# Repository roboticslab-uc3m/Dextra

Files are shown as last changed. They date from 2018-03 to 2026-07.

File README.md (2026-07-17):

# Dextra

Dextra is a printable robotic hand with the size of a human hand. This project was initially started by A. Villoslada to build a replicable and low cost alternative to current robotic hand prostheses. However, I think this device has more potential uses, for example in robotics research (humanoid robotics, mobile platforms with manipulation capabilities) or in education, fields that could benefit from the existence of a cheap and easy to repair robotic hand, a robotic device that is replicable and hackable, and simple but functional.

<p align="center">

</p>

There is more information about Dextra on its [hackaday.io project page](https://hackaday.io/project/9890-dextra).

## Dextra TPMG90

J. Gago Industrial Technologies Engineering Bachelor's Degree Final Project comprises the development and integration of an anthropomorphic robotic hand in the humanoid robot TEO. TEO is a household companion developed by RoboticsLab, at Carlos III University of Madrid, whose current robotic hands lack the necessary functionality for the tasks that require high manual dexterity, like fabric manipulation.

<p align="center">
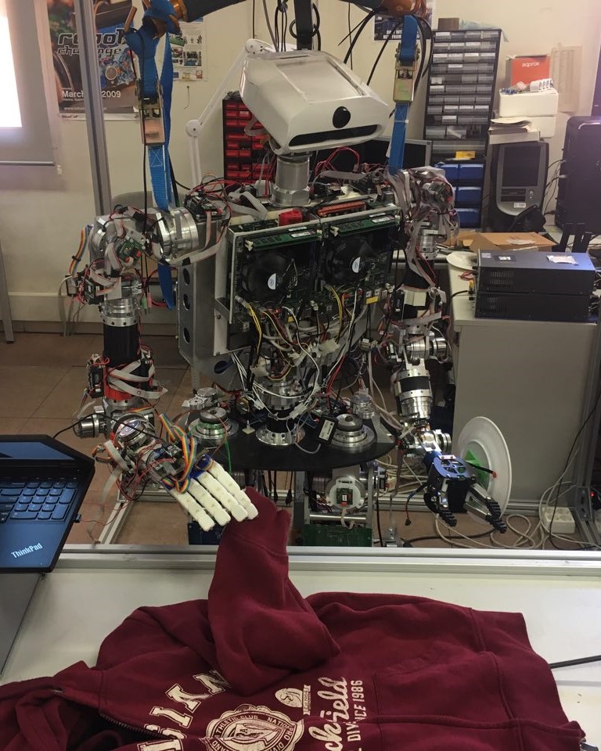
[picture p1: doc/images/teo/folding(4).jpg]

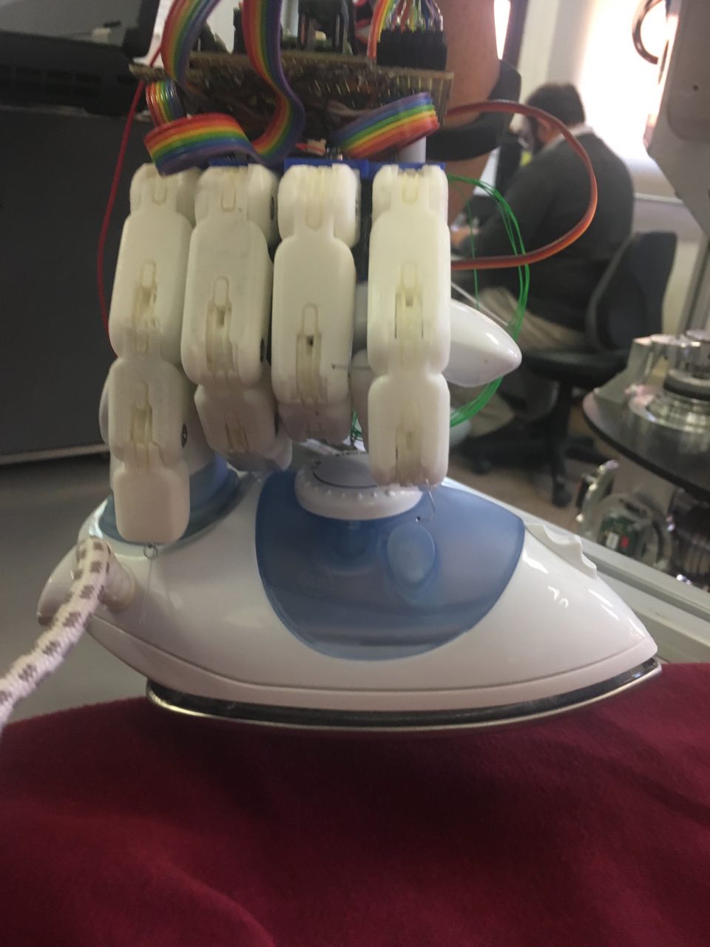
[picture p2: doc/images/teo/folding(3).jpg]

</p>

The scope of the proposed objectives is achieved through the development and study of several versions of the selected hand at the mechanical, electronic and software level. Multiple experiments are developed to evaluate the effectiveness of the robotic hand. In addition, the regulatory technical framework and the socio-economic environment of the project are evaluated, so that it complies satisfactorily with the established restrictions and adjusts to the current social and economic context.

<p align="center">
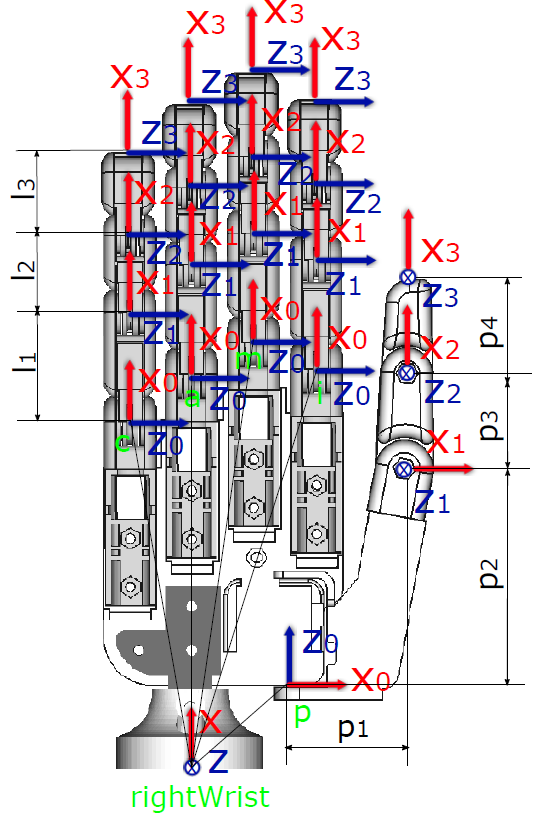
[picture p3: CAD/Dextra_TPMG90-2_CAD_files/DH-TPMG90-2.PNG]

</p>

The project is oriented to numerous additional studies around their behavior in the humanoid, contemplating the expansion of the TEO functions in relation to the versatility provided by his new fully functional hands.

<p align="center">
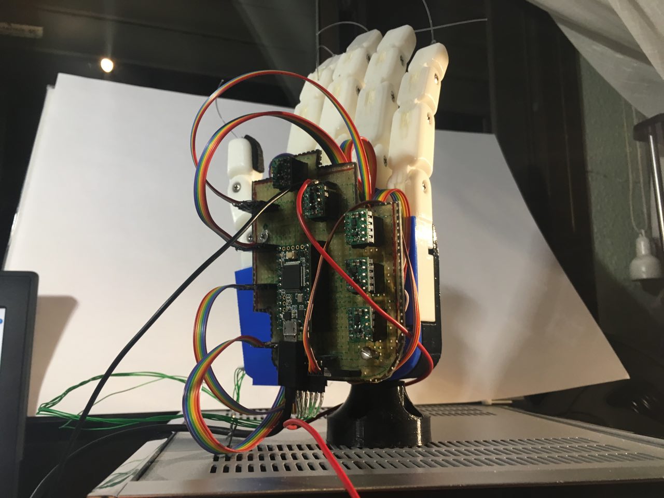
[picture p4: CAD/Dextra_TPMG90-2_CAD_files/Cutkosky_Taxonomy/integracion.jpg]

</p>

## Dextra TPMG90S

Miguel Alache Manchado followed up on Jennifer Gago's work in his Bachelor's Degree Final Project (Industrial Electronics Engineering and Automation), notably improving the 3D CAD and PCB designs. This iteration is dubbed TPMG90S due to the replacement of the TPMG90 servomotor with this new model.

Although compatibility with TEO is preserved, the aim was to mount this hand on the ABB CRB 15000-5 "GoFa" collaborative robot arm.

<p align="center">
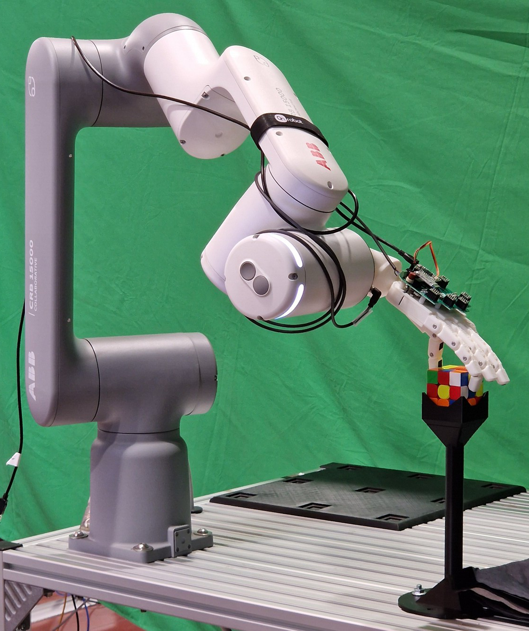
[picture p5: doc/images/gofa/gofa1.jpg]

</p>

## Useful documents

The assembly instructions for the original Dextra can be found [here](doc/dextra_assembly_instructions.pdf).

## Project index

* [CAD](CAD) - Printable parts
* [Control](Control) - Code for different control methods (EMG, GUI)
* [doc](doc) - Documentation files
* [Firmware](Firmware) - Main program and libraries that make Dextra move
* [PCB](PCB) - PCB design files
* [Schematics](Schematics) - Electronic schematics of Dextra Original, TPMG90-1 and TPMG90-2

## License

<a rel="license1" href="https://www.gnu.org/licenses/gpl-3.0.html">GNU License</a>  

Code is licensed under the [GPL v3 License](https://www.gnu.org/licenses/gpl-3.0.html). The rest of the work is licensed under the [Creative Commons Attribution-ShareAlike 4.0 International License](http://creativecommons.org/licenses/by-sa/4.0/).

## See also

* [dextra-yarp-devices](https://github.com/roboticslab-uc3m/dextra-yarp-devices) - YARP plugins for Dextra control board

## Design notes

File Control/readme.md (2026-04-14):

The Dextra Control GUI is designed using [Kivy](https://kivy.org/#home). Besides having Python installed, this library and its dependencies are required to run the application. The application uses both the *.py* and the *.kv* files, and they need to be in the same folder.

To run the control GUI, connect the microcontroller running the Dextra firmware to a USB port of the computer, and run:

```bash
~/Dextra$ cd Control
~/Dextra/Control$ python3 DextraControl.py
```

First, the device to which we want to communicate (the microcontroller running the Dextra firmware) has to be selected from a dropdown list. Once the desired device is selected (in this case the one connected to COM4; in this example the app is running on a Windows PC), we click on the connect button. If there is no device connected to the PC, or no device is selected from the dropdown list, an error message is displayed.

<p align="center">
        
</p>

If the connection is successful, we can select the *Control panel* tab. In this tab, we can control the position of each finger and the abduction angle of the thumb. The position values can be inputted by using the text boxes or by moving the sliders.

<p align="center">
    
</p>

To stop communicating with the microcontroller, we select the *Connection* tab and click the disconnect button.

<p align="center">
    
</p>

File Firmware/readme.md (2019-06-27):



To upload the firmware to one of the supported boards, use [platformio](http://platformio.org/).

For Teensy 3.1 (Arduino-compatible board):
```bash
~/Dextra$ cd Firmware/Teensy31
~/Dextra/Firmware/Teensy31$ platformio run --target upload
```

Make sure you have sufficient rights to interface with the Teensy H/W. This can be accomplished by copying `49-teensy.rules` to `/etc/udev/rules.d/`.

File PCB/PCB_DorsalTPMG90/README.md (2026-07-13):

# PRINTED CIRCUIT BOARD FOR DEXTRA TPMG90-2
## OBJECTIVE
The main objective is to design a Printed Circuit Board (PCB) to replace the breadboard, shown bellow, in the back of the right robotic hand of the humanoid robot TEO. A PCB is a board or card that electrically connects and mechanically supports electrical components. These connections are made with a series of conductive tracks or traces (usually copper ones). This copper is laminated onto or in between sheets of non-conductive material like fiberglass.

<p align="center">
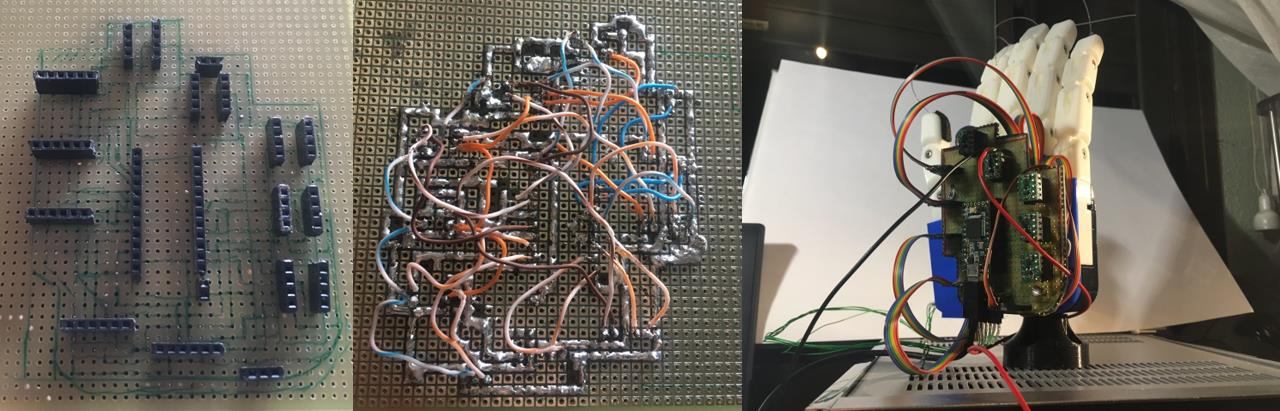
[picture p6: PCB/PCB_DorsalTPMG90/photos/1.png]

</p>

## CONSIDERATIONS

Points below were taken into account during the design process:
* PCB shape and size
* User interfaces
* PCB layers
* Ground layers
* Traces width

Regarding PCB traces:
* 45° angles shorten the electrical path between components.
* High speed logic signals (above 200 MHz) can get reflected off the back of the angle, Causing interference.
* 90o has the likelihood of being etched narrower than your standard trace width.
* 90o traces back might not be fully etched, could cause shorts.

<p align="center">
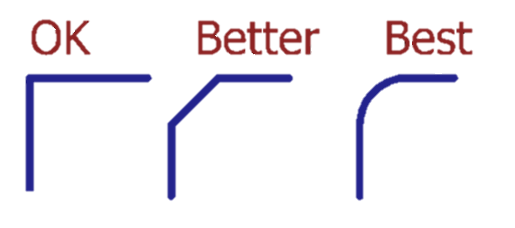
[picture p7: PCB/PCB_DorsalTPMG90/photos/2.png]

</p>

## MATERIALS

The design of the PCB is going to be done using KiCad, an open-source software tool which can be considered mature enough to be used for the successful development and maintenance of complex electronics boards.

<p align="center">
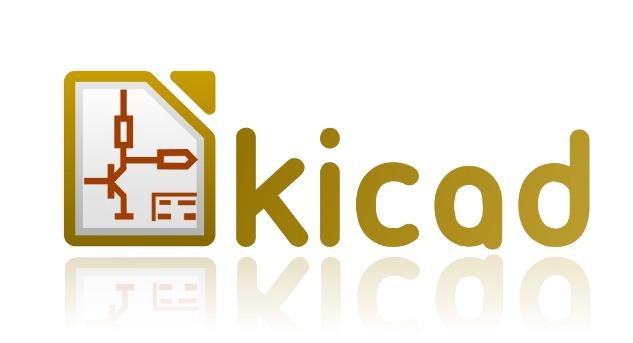
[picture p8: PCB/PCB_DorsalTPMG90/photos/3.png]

</p>

## WORKFLOW

The KiCad workflow is comprised of two main tasks: drawing the schematic and laying out the board. Both a schematic component library and a PCB footprint library are necessary for these two tasks. In the following figure, the workflow followed during this project is shown.

<p align="center">
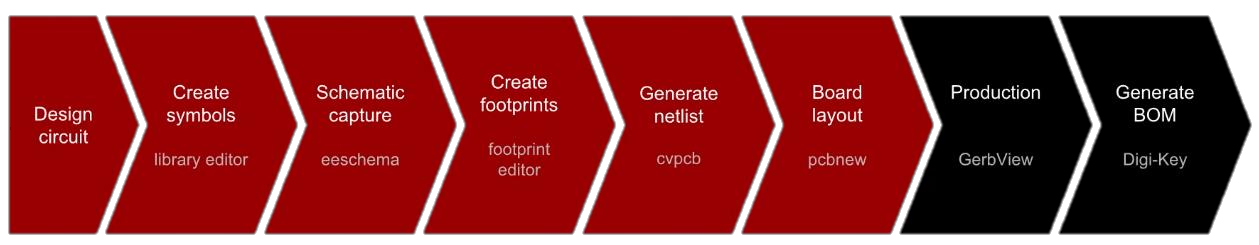
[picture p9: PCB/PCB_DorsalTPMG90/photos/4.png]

</p>

Any PCB design is divided in three main steps:
* Schematics design
* PCB design (routing, components and PCB dimensions)
* BOM list (Bill of materials): actual components to be used (in case connectors of any type have to be considered: USB, expansion jumper connectors...)

### 1. SCHEMATIC DESIGN

It is assumed that each components is a box with inputs and outputs. The schematic contains the connections between the pins of the boxes without considering the dimensions of any component. To start with the design it is needed the datasheet with the pinout description for each component (in our case the drivers, the Servo and the microprocessor).

* DRV8838 Single Brushed DC Motor Driver Carrier

<p align="center">
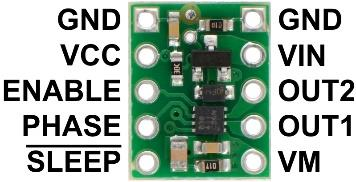
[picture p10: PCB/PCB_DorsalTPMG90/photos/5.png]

</p>

* Microcontroller: Teensy 3.2

<p align="center">
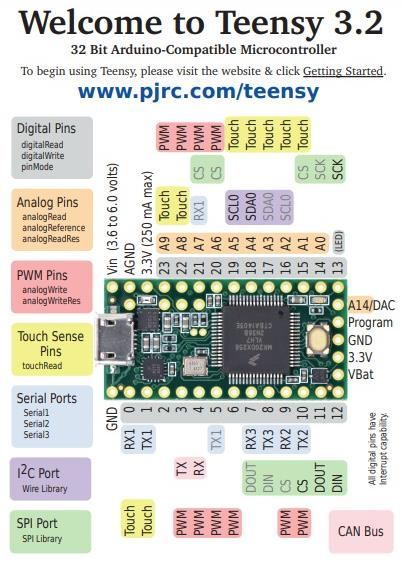
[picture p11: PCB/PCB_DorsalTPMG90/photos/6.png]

</p>

* Servo TowerPro MG90 (directly connected to the PCB)

<p align="center">
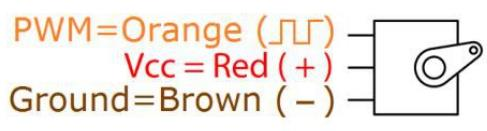
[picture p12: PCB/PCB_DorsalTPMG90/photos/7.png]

</p>

The starting point of this project is based on the connections shown in the schematic depicted in the figure bellow, and available in this GitHub repository (Dextra/Schematics/DEXTRA_TPMG90-2.png). In this design each component is represented as a pair of standard connectors (one for each side of the component). Although it can be easily understood, it is preferable to create specific symbols for each component to facilitate PCB layout in following steps.

<p align="center">
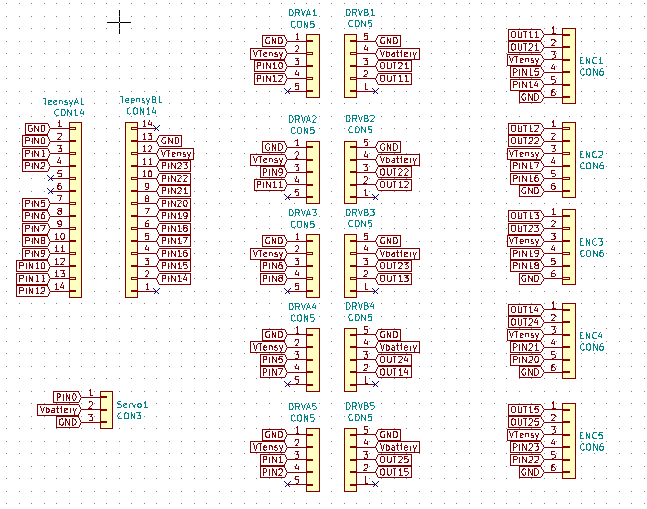
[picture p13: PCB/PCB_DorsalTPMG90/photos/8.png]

</p>

The symbols for the components are stored in two different schematic libraries located in “Project folder/Libraries/dorsalSchematic_Components/ and are named: <b>DRV8838_Pololu.lib</b> and <b>teensy.lib</b>. In the case of the driver, the components were created manually using KiCad and in the case of the Teensy it was downloaded from a GitHub [repository](https://github.com/XenGi/teensy_library). The pair of figures bellow show the schematic symbols for Teensy 3.2 and Pololu Driver, respectively.

<p align="center">
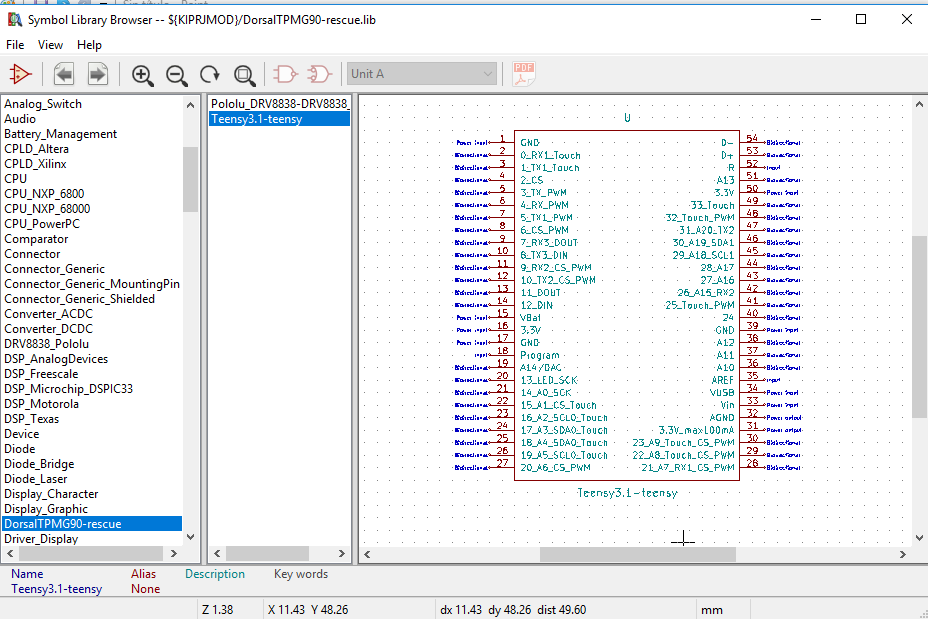
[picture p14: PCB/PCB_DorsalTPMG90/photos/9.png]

</p>

<p align="center">
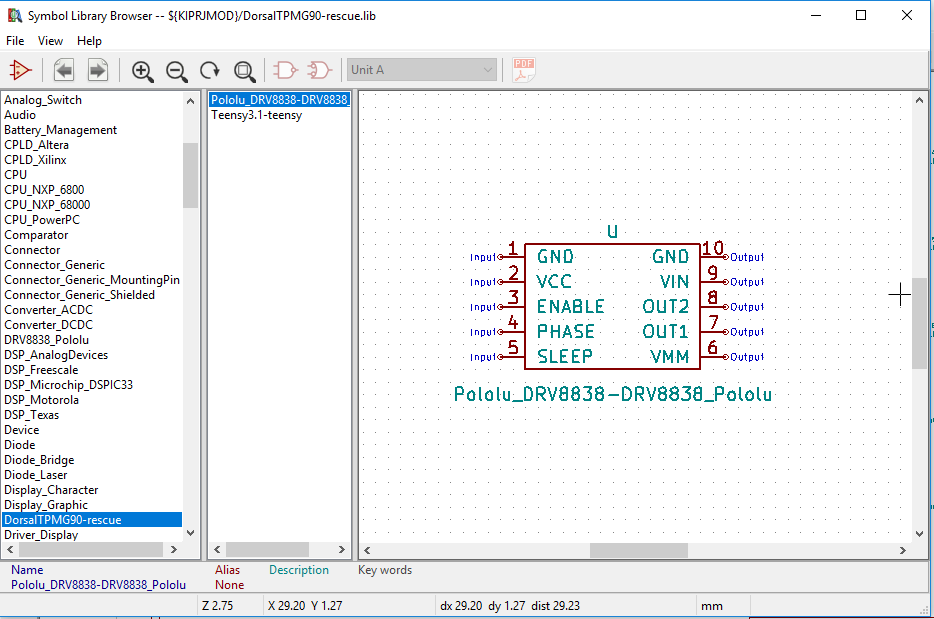
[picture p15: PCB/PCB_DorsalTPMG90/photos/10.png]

</p>

The final schematic is shown bellow. Standard connectors have been used for the 6 encoders, the Servo and the battery input. For the drivers and the Teensy the symbols already mentioned are shown. In order to establish the connections global labels, no connection flags, and power ports have been used. Final step is <b>to annotate the components and create the Netlist</b> which is later import in the PCB design.

<p align="center">
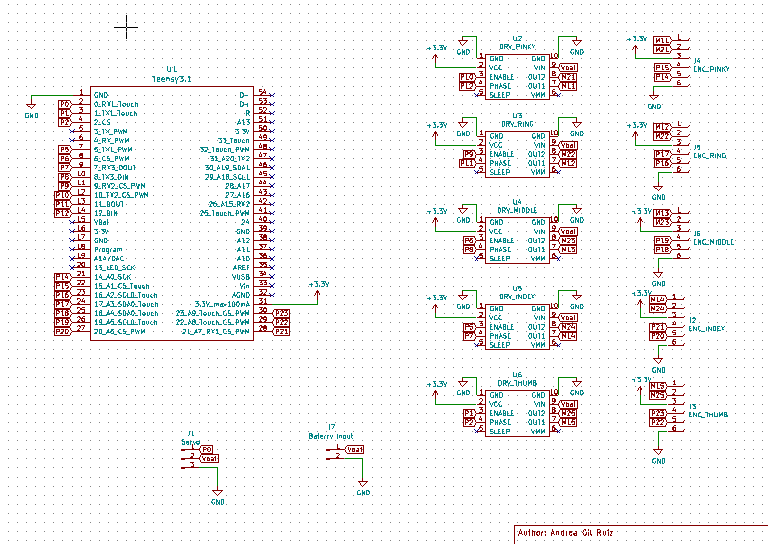
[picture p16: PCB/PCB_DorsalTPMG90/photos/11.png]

</p>

### 2. PCB DESIGN

This is probably the most difficult part of the project.. Steps followed are:

1. Assign footprints to each symbol in the schematic design.
2. Import Netlist with the connections
3. PCB layout design:
    1. Draw PCB edges and holes according to CAD specifications.
    2. Place each component in specific locations and orientations to facilitate trace routing
    3. Route components: use front and back Cu layers because there are too many connections; use vias when needed; increase trace width depending on maximum current specifications.
    4. Fill Front and Back Cu layers with GND and VCC (+3.3V), respectively.
4. Define Design Rules according to Oshpark prototypes and run Design Rules Check at the end of the layout to avoid errors.
5. Place text and Logos to indicate component name and orientation during assembly.

The main difference between footprints and symbols is that footprints define the physical interface between the PCB and the component (land pattern) and include other information (outline, polarization mark, reference...) while symbols are just a representation of the component (they abstract its function) showing the pins.

In order to assign each correspondent footprint to the symbols, a new library of footprints has been created with the corresponding footprints for the drivers and the Teensy. In the folder “Project folder */Libraries/dorsalPCB_Components.pretty* / (folders ending in .pretty are recognized by KiCad as footprint library) are 3 footprints. The footprint for the driver has been
created manually using the dimension specification in its datasheet (shown below).

<p align="center">
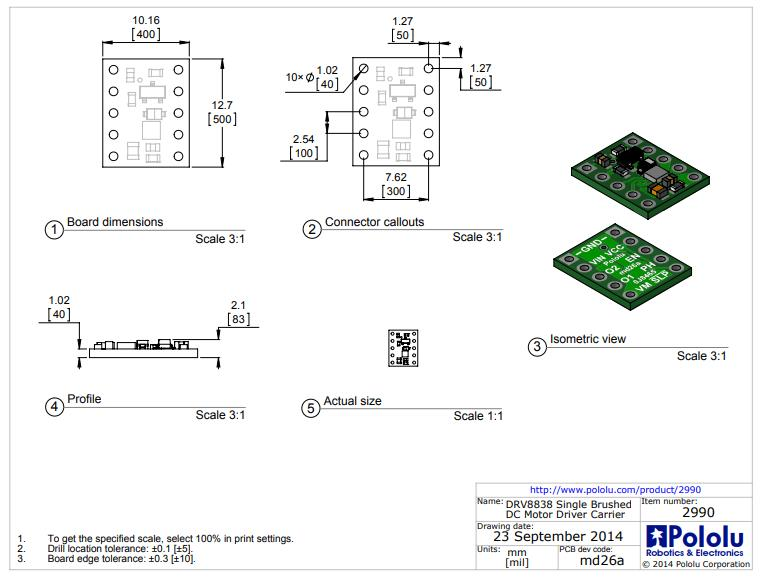
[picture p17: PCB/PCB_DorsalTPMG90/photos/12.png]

</p>

<p align="center">
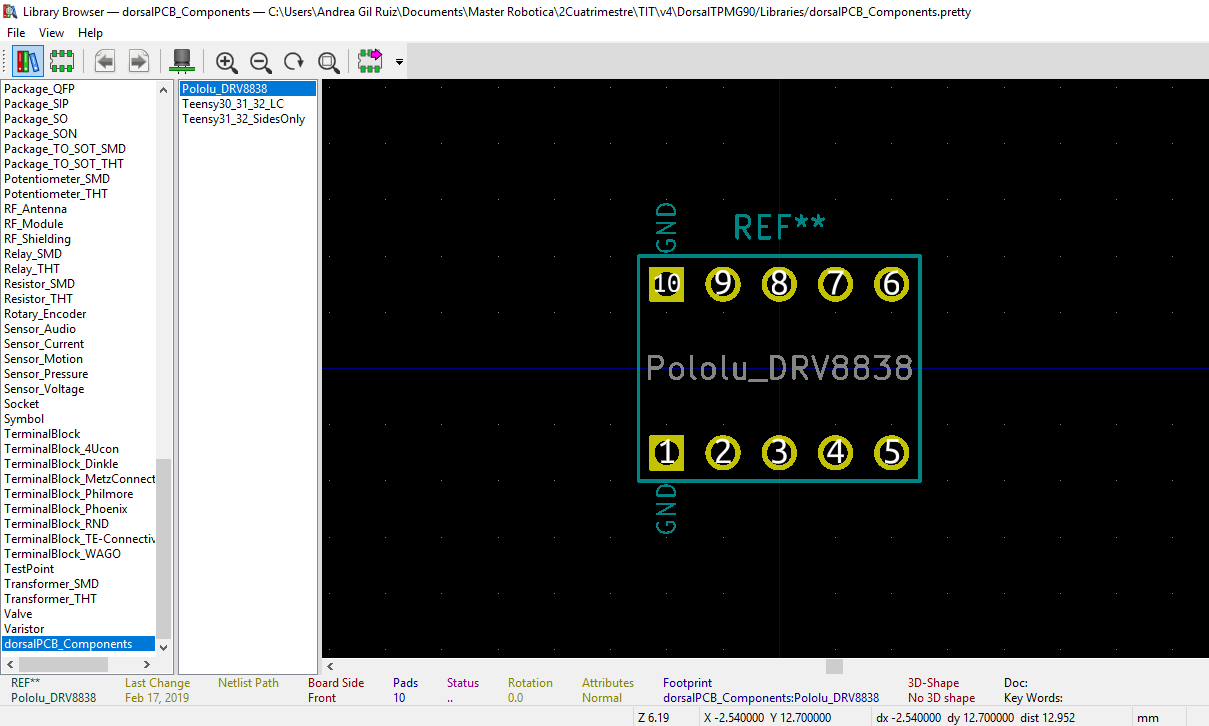
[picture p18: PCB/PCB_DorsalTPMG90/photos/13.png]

</p>

The footprint for the Teensy has been downloaded for the GitHub [repository](https://github.com/XenGi/teensy.pretty) and edited in KiCad to delete the pins which are not used in the design. Only pins on sides have been kept, as shown in the figures below, to facilitate routing.

<p align="center">
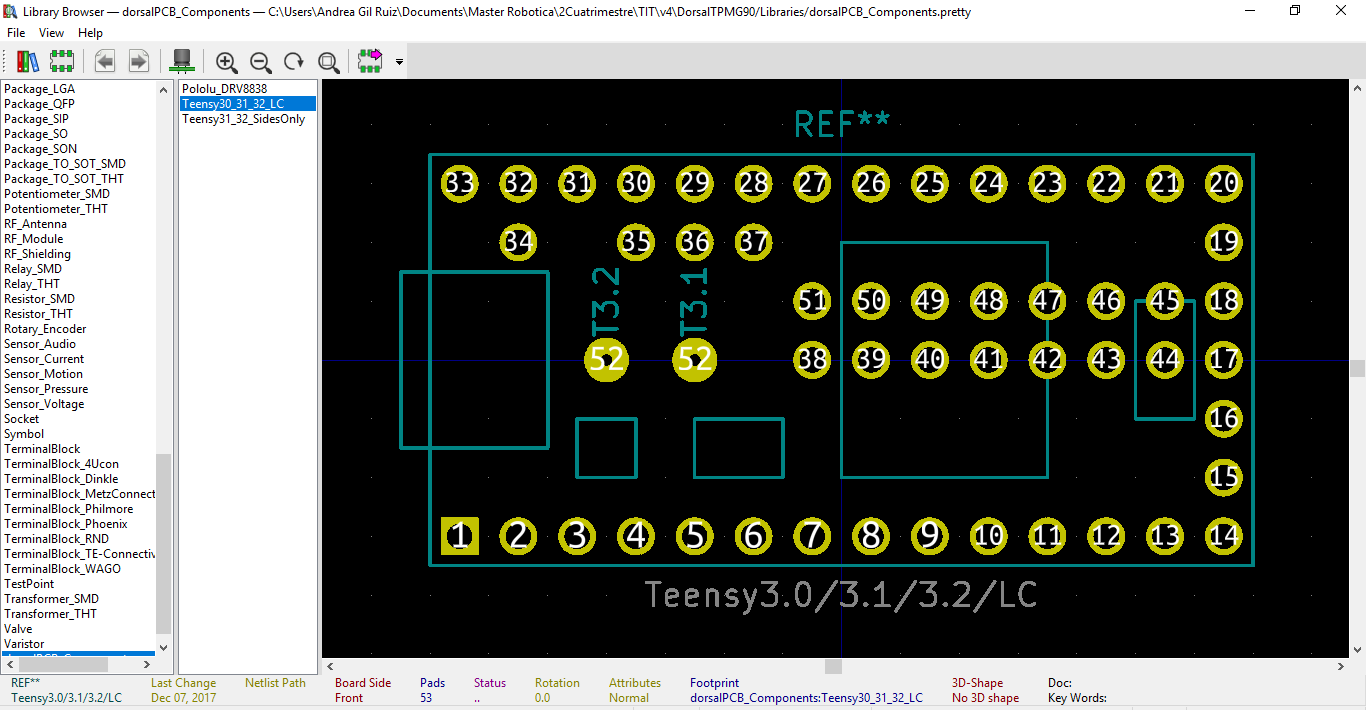
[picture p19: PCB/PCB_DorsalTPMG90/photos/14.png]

</p>

<p align="center">
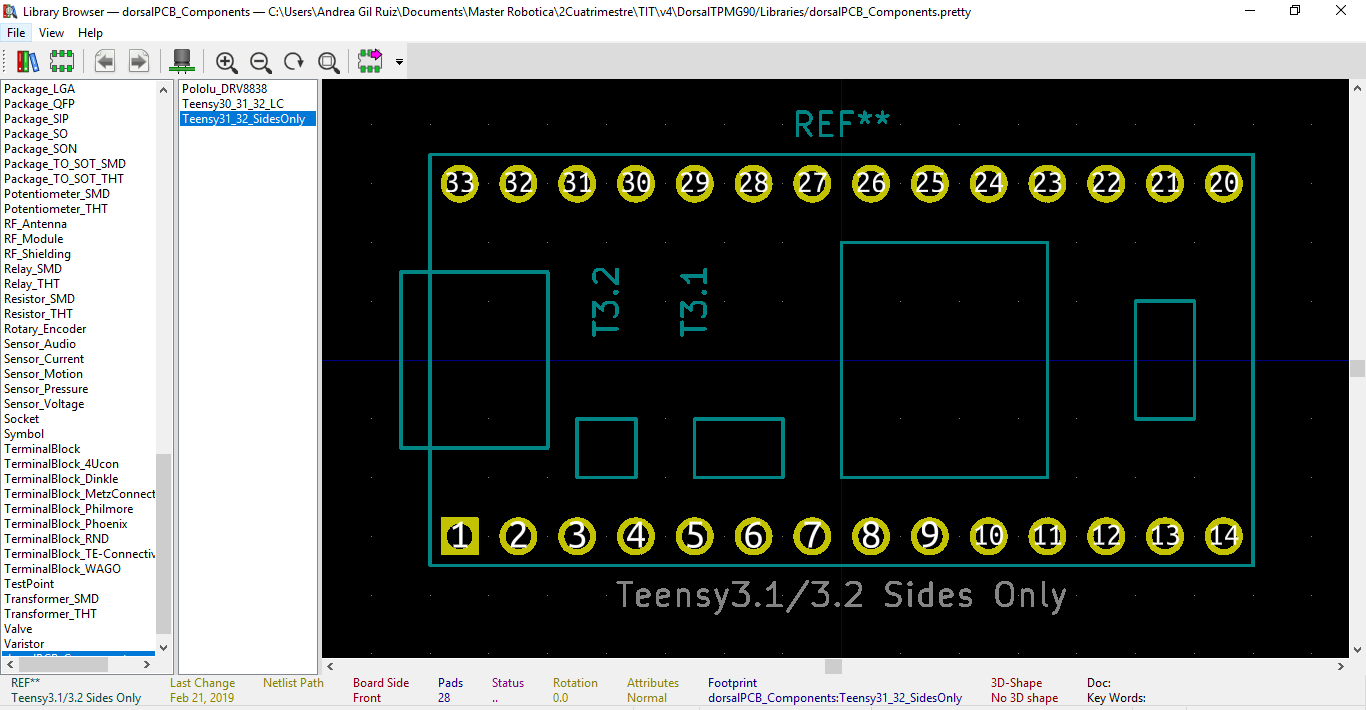
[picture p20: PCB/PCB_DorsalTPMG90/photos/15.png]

</p>

Once the footprints have been assigned it is possible to read the schematic Netlist and start designing the PCB. Steps follow for the design are explained below:

* Place the components into the space of the designed board. For this step, the CAD file of the dorsal is used (path:  Dextra/Dextra_TPMG90-2_CAD_files/dorsalTPMG90-2.FCStd). The dimensions are specified in the figures below.

<p align="center">
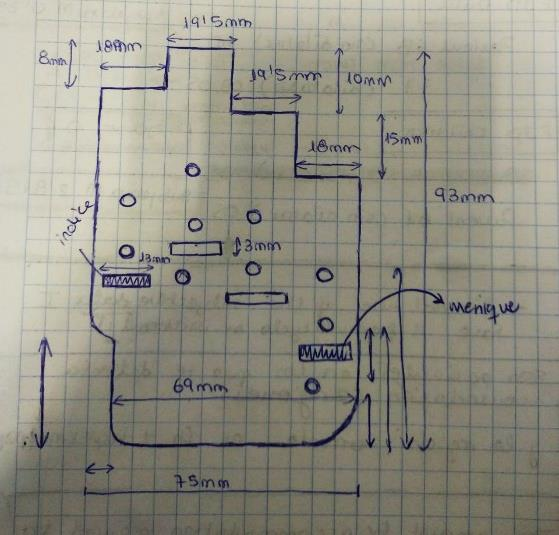
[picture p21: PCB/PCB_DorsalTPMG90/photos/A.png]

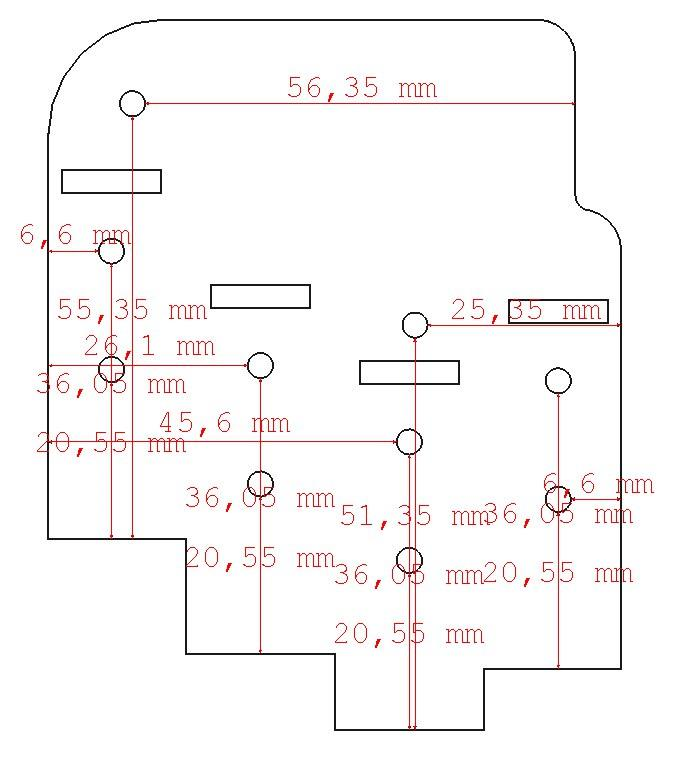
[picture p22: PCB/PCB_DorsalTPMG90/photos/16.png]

</p>

<p align="center">
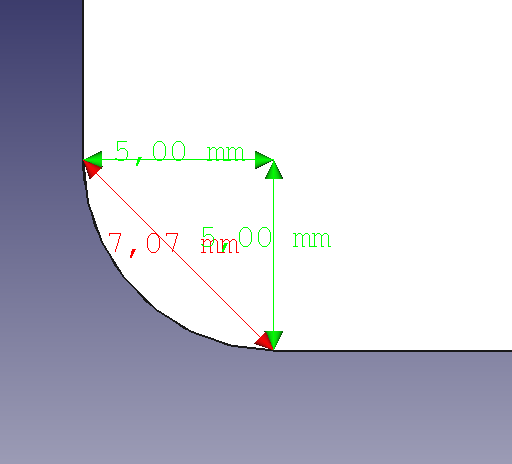
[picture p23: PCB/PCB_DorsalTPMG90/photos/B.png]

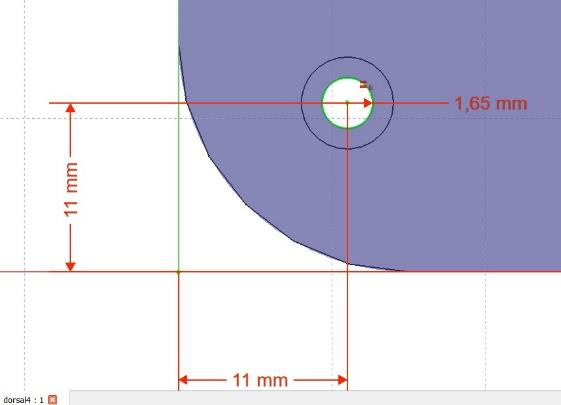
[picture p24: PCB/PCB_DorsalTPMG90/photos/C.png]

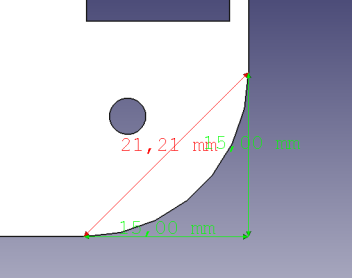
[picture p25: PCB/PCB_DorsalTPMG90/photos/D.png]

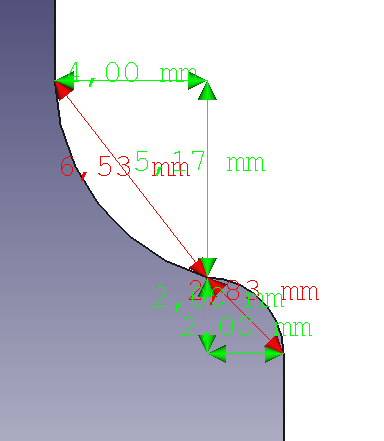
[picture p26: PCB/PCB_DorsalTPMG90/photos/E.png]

</p>

The shape and distribution have been drawn in the edge cap layer (See Annex) using graphic lines and circles (and using different grids to draw an accurate design). (Defining the outline)

<p align="center">
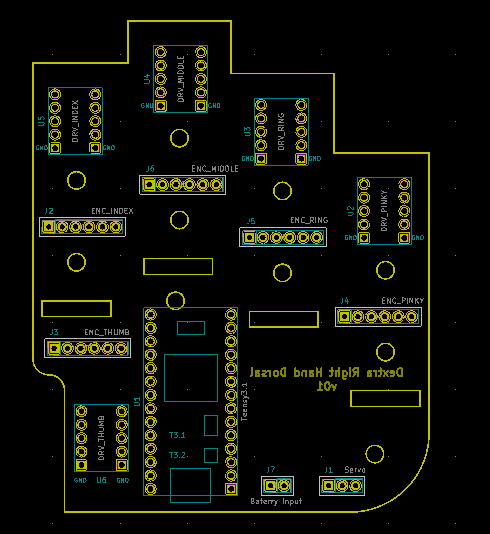
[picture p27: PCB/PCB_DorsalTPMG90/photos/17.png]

</p>

The next step is drawing traces to make air wires disappear (checking always the design rules check DRC). If there are any issues with the layout (such as traces being too close together) it will appear there, as well as the connections which should be made with copper traces. Traces have been drawn in front cupper layer and back cupper layer, using only 45 degree bends to make connections. Considerations:

* Power lines /Power traces (VBat in our case) are larger than signal traces as they need to carry much more current. Theoretically the trace supplying power needs to support up to 1.7 A, according to Pololu DRV8838 datasheet. Trace width calculator (0.676 mm).
* Connect first pads which are close together.
* Traces have not been used to connect the Ground and VCC (+3.3V) nodes as a Cu pour will be used to make those connections. A copper pour is an area in the PCB that is filled with copper. The pour is usually connected to DC voltage (Back Cu layer in our design) and Ground (Front Cu layer in our design). Its use reduces radio emissions from traces
that are surrounded by this pour especially in circuits with higher frequencies.
* It is not possible to draw a trace across another trace or a pad, use Vias in these situations.
* Use 45º angles (many older board houses could only manufacture straight lines on that angles). Also, when you get up to higher frequencies (above 1GHz) reflections could be introduced with hard 90º bends (not our case).
* Try to avoid acute angles where copper connects (older board manufacturing processes used harsh chemicals to etch away copper). Traces with bends of less than 90º would capture some of these chemicals (acid trap).

<p align="center">
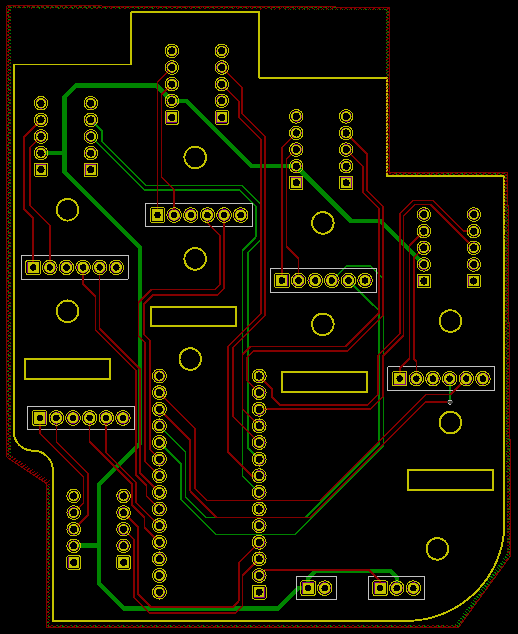
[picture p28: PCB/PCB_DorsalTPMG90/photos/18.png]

</p>

In the current design two pour areas have been used: one for the power (+3V3) in the back layer and the ground in the front layer. Also, connections between pads in both layers and one vias. The final result is shown in the next figure.

<p align="center">
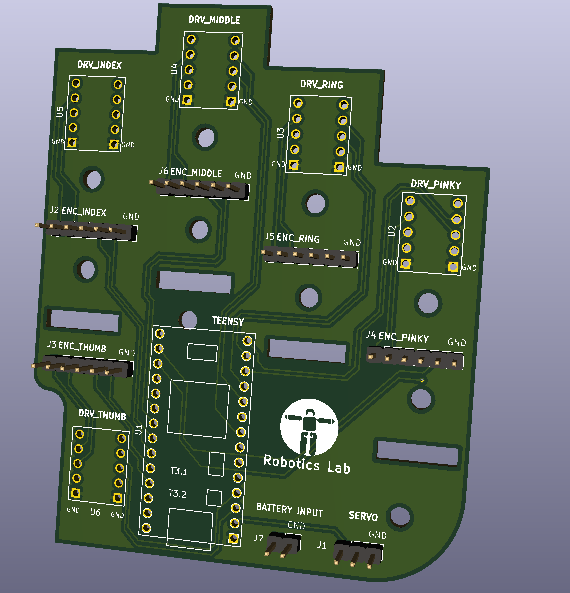
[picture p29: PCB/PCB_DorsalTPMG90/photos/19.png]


</p>

## Annex: Layers information

In KiCad the following layers are available.

* Layers that have a front and back version start with F. (for front) and B. (for back)
* The F.Cu and B.Cu layers are the copper layers
    * If there are additional copper layers they use the names In [number].Cu by default
    * The names for copper layers can be changed by the designer.
* F.Silk and B.Silk define artwork on the silkscreen layers.
    * Typically this is the white artwork printed on the board.
* F.Mask and B.Mask define the area free of [soldermask](https://en.wikipedia.org/wiki/Solder_mask) 193.
    * It is the negative of the resulting film that covers the board.
* F.Paste and B.Paste define the area that will be covered with [solder paste](https://en.wikipedia.org/wiki/Solder_paste) 88 (In datasheets often called stencil)
    * Used for [reflow soldering](https://en.wikipedia.org/wiki/Reflow_soldering) 32 of surface mounted devices.
* Edge.cuts: This layer is used to communicate with the manufacturer what the final board shape should look like.
    * The edge-cut is must not contain self intersections
    * Polygons on the edge-cut must be continuous and closed.
    * It is allowed to have internal cutouts
* F.Adhes and B.Adhes are layers to define adhesive (=glue) areas.
    * Only needed if components are on the bottom side during reflow soldering. (And even with components on the bottom it is not always needed. Check with your manufacturer if you need to define it for your board.)
* F.CrtYd and B.CrtYd are used to define a courtyard area.
    * The courtyard defines where no other component should be placed.
        * The size of this area depends on your manufacturing capabilities.
        * It also depends on your needs. (If you want the possibility to rework the pcb, you might need a larger area compared to when you do not plan to do this.)
        * The rules used in the official lib are defined in the [KLC - Rule](http://kicad-pcb.org/libraries/klc/F5.3/) F5.3 87 and are closely aligned to industry standards.
    * In KiCad 4.0.x courtyard violations are not checked by the design rule check
* F.Fab and B.Fab are documentation layers.
    * These are intended to be used for communicating with board assembly houses and for user documentation.
* Dwgs.User and Cmts.User are used for user drawings and comments.
    * In the official lib this layer is used to communicate with the user of footprints. (Example to tell them where to place keepout areas as they are not directly supported by KiCad in footprints)
* Eco1 and Eco2 are layers with no specific defined purpose. (The user can use them for whatever they want. They are not used in footprints supplied by the official lib.)
* Margin layer: Is there to define a margin relative to the edge cut.
    * There is no DRC check to verify that no copper feature violates the margin definition.

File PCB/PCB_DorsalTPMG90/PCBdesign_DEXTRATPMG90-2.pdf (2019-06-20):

## PRINTED CIRCUIT BOARD FOR DEXTRA TPMG90-2

OBJECTIVE

The main objective is to design a Printed Circuit Board (PCB) to replace the breadboard, shown in Figure 1, in the back of the right robotic hand of the humanoid robot TEO. A PCB is a board or card that electrically connects and mechanically supports electrical components. These connections are made with a series of conductive tracks or traces (usually copper ones). This copper is laminated onto or in between sheets of non-conductive material like fiberglass.


Fig. 1 Breadboard present in Dextra TPMG90-2

CONSIDERATIONS

Points below were taken into account during the design process:
- PCB shape and size
- User interfaces
- PCB layers
- Ground layers
- Traces width

Regarding PCB traces:
- 45° angles shorten the electrical path between components.
- High speed logic signals (above 200 MHz) can get reflected off the back of the angle, causing interference.
- 90º has the likelihood of being etched narrower than your standard trace width.
- 90º traces back might not be fully etched, could cause shorts.


Fig. 2 PCB traces

MATERIALS

The design of the PCB is going to be done using KiCad, an open-source software tool which can be considered mature enough to be used for the successful development and maintenance of complex electronics boards.

WORKFLOW


The KiCad workflow is comprised of two main tasks: drawing the schematic and laying out the board. Both a schematic component library and a PCB footprint library are necessary for these two tasks. In Figure 3, the workflow followed during this project is shown.


Fig. 3 Steps followed and stand-alone software tools in KiCad

Any PCB design is divided in three main steps:

- Schematics design
- PCB design (routing, components and PCB dimensions)
- BOM list (Bill of materials): actual components to be used (in case connectors of any type have to be considered: USB, expansion jumper connectors...)

### 1. SCHEMATIC DESIGN

It is assumed that each components is a box with inputs and outputs. The schematic contains the connections between the pins of the boxes without considering the dimensions of any component.

To start with the design it is needed the datasheet with the pinout description for each component (in our case the drivers, the Servo and the microprocessor).

- DRV8838 Single Brushed DC Motor Driver Carrier


Fig. 4 Pins of each driver

- Microcontroller: Teensy 3.2


Fig. 5 Pins of the microcontroller

- Servo TowerPro MG90 (directly connected to the PCB)


Fig. 6 Pins of the Servo

The starting point of this project is based on the connections in the schematic shown in Figure 7, and available in this GitHub link. (https://github.com/jgagom/Dextra/blob/dextraTPMG90/Schematics/DEXTRA_TPMG90-2.png) In this design each component is represented as a pair of standard connectors (one for each side of the component). Although it can be easily understood, it is preferable to create specific symbols for each component to facilitate PCB layout in following steps.


Fig. 7 First Schematic

The symbols for the components are stored in two different schematic libraries located in “Project folder/Libraries/dorsalSchematic_Components/ and are named: DRV8838_Pololu.lib and teensy.lib. In the case of the driver, the components were created manually using KiCad and in the case of the Teensy it was downloaded from a GitHub repository. (https://github.com/XenGi/teensy_library) Figures 8 and 9, show the schematic symbols for Teensy 3.1 and Pololu Driver respectively.

Fig. 8 Symbol of the Teensy


Fig. 9 Symbol of the driver

The final schematic is shown in Figure 10. Standard connectors have been used for the 6 encoders, the Servo and the battery input. For the drivers and the Teensy the symbols already mentioned are shown. In order to establish the connections global labels, no connection flags, and power ports have been used. Final step is to annotate the components and create the Netlist which is later import in the PCB design.

Fig. 10 Final Schematic version

### 2. PCB DESIGN

This is probably the most difficult part of the project.. Steps followed are:

1. Assign footprints to each symbol in the schematic design.
2. Import Netlist with the connections
3. PCB layout design:
a. Draw PCB edges and holes according to CAD specifications.
b. Place each component in specific locations and orientations to facilitate trace routing
c. Route components: use front and back Cu layers because there are too many connections; use vias when needed; increase trace width depending on maximum current specifications.
d. Fill Front and Back Cu layers with GND and VCC (+3.3V), respectively.
4. Define Design Rules according to Oshpark prototypes and run Design Rules Check at the end of the layout to avoid errors.
5. Place text and Logos to indicate component name and orientation during assembly.

The main difference between footprints and symbols is that footprints define the physical interface between the PCB and the component (land pattern) and include other information (outline, polarization mark, reference…) while symbols are just a representation of the component (they abstract its function) showing the pins.

In order to assign each correspondent footprint to the symbols, a new library of footprints has been created with the corresponding footprints for the drivers and the Teensy. In the folder “Project folder/Libraries/dorsalPCB_Components.pretty / (folders ending in .pretty are recognized by KiCad as footprint library) are 3 footprints. The footprint for the driver has been created manually using the dimension specification in its datasheet (shown below).


Fig. 11 Dimensions of the driver

Fig. 12 Footprint of each driver

The footprint for the Teensy has been downloaded for the GitHub repository (https://github.com/XenGi/teensy.pretty) and edited in KiCad to delete the pins which are not used in the design. Only pins on sides have been kept, as shown in the figures below, to facilitate routing.


Fig. 13 Footprint of the microcontroller with all pins

Fig. 14 Footprint of the microcontroller with the neccesary pins

Once the footprints have been assigned it is possible to read the schematic Netlist and start designing the PCB. Steps follow for the design are explained below:

- Place the components into the space of the designed board. For this step, the CAD file (https://github.com/jgagom/Dextra/blob/dextraTPMG90/Dextra_TPMG90-2_CAD_files/dorsalTPMG90-2.FCStd) of the dorsal part of the hand is used. The dimensions are specified in the figures below.


The shape and distribution have been drawn in the edge cap layer (See Annex) using graphic lines and circles (and using different grids to draw an accurate design). (Defining the outline)

Fig. 16

Fig. 15

Fig. 18

Fig. 17

Fig. 20

Fig. 19


Fig. 21 Edge cap layer design

The next step is drawing traces to make air wires disappear (checking always the design rules check DRC). If there are any issues with the layout (such as traces being too close together) it will appear there, as well as the connections which should be made with copper traces. Traces have been drawn in front cupper layer and back cupper layer, using only 45 degree bends to make connections, see Figure 22. Considerations:

- Power lines /Power traces (VBat in our case) are larger than signal traces as they need to carry much more current. Theoretically the trace supplying power needs to support up to 1.7 A, according to Pololu DRV8838 datasheet. Trace width calculator (0.676 mm).
- Connect first pads which are close together.
- Traces have not been used to connect the Ground and VCC (+3.3V) nodes as a Cu pour will be used to make those connections. A copper pour is an area in the PCB that is filled with copper. The pour is usually connected to DC voltage (Back Cu layer in our design) and Ground (Front Cu layer in our design). Its use reduces radio emissions from traces that are surrounded by this pour especially in circuits with higher frequencies.
- It is not possible to draw a trace across another trace or a pad, use Vias in these situations.
- Use 45º angles (many older board houses could only manufacture straight lines on that angles). Also, when you get up to higher frequencies (above 1GHz) reflections could be introduced with hard 90º bends (not our case).
- Try to avoid acute angles where copper connects (older board manufacturing processes used harsh chemicals to etch away copper). Traces with bends of less than 90º would capture some of these chemicals (acid trap).


In the current design two pour areas have been used: one for the power (+3V3) in the back layer and the ground in the front layer. Also, connections between pads in both layers and one vias. The final result is shown in the next figure (Fig 23).

Fig. 22 Traces in the PCB are drawn using 45º


Fig. 23 3D-view of the PCB

Annex: Layers information

In KiCad the following layers are available.

- Layers that have a front and back version start with F. (for front) and B. (for back)
- The F.Cu and B.Cu layers are the copper layers
- If there are additional copper layers they use the names In[number].Cu by default
- The names for copper layers can be changed by the designer.
- F.Silk and B.Silk define artwork on the silkscreen layers.
- Typically this is the white artwork printed on the board.
- F.Mask and B.Mask define the area free of soldermask 193. (https://en.wikipedia.org/wiki/Solder_mask)
- It is the negative of the resulting film that covers the board.
- F.Paste and B.Paste define the area that will be covered with solder paste 88 (https://en.wikipedia.org/wiki/Solder_paste) (In datasheets often called stencil)
- Used for reflow soldering 32 (https://en.wikipedia.org/wiki/Reflow_soldering) of surface mounted devices.
- Edge.cuts: This layer is used to communicate with the manufacturer what the final board shape should look like.
- The edge-cut is must not contain self intersections
- Polygons on the edge-cut must be continuous and closed.
- It is allowed to have internal cutouts
- F.Adhes and B.Adhes are layers to define adhesive (=glue) areas.
- Only needed if components are on the bottom side during reflow soldering. (And even with components on the bottom it is not always needed. Check with your manufacturer if you need to define it for your board.)
- F.CrtYd and B.CrtYd are used to define a courtyard area.
- The courtyard defines where no other component should be placed.
- The size of this area depends on your manufacturing capabilities.
- It also depends on your needs. (If you want the possibility to rework the pcb, you might need a larger area compared to when you do not plan to do this.)
- The rules used in the official lib are defined in the KLC - Rule
F5.3 87 (http://kicad-pcb.org/libraries/klc/F5.3/) and are closely aligned to industry standards.
- In KiCad 4.0.x courtyard violations are not checked by the design rule check
- F.Fab and B.Fab are documentation layers.
- These are intended to be used for communicating with board assembly houses and for user documentation.
- Dwgs.User and Cmts.User are used for user drawings and comments.
- In the official lib this layer is used to communicate with the user of footprints. (Example to tell them where to place keepout areas as they are not directly supported by KiCad in footprints)
- Eco1 and Eco2 are layers with no specific defined purpose. (The user can use them for whatever they want. They are not used in footprints supplied by the official lib.)
- Margin layer: Is there to define a margin relative to the edge cut.
- There is no DRC check to verify that no copper feature violates the margin definition.

TUTORIALS

Creation of a PCB in 20 mins:

https://www.youtube.com/watch?v=zK3rDhJqMu0

Several videos with extended explanations of each step: (Recommended!)

https://www.youtube.com/watch?v=gIf8sdd-JL4&list=PLEBQazB0HUyR24ckSZ5u05TZHV9khgA1O (https://www.youtube.com/watch?v=gIf8sdd-JL4&list=PLEBQazB0HUyR24ckSZ5u05TZHV9khgA1O)

Add a logo/image:

https://www.youtube.com/watch?v=CAlBWQTAWJU

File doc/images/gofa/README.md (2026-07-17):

<p align="center">


</p>

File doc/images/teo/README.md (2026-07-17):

<p align="center">


</p>

<p align="center">


</p>

<p align="center">


</p>

<p align="center">


</p>

<p align="center">


</p>

<p align="center">


</p>

<p align="center">


</p>

<p align="center">


</p>



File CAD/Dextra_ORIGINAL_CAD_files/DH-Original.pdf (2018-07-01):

x

x


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
handRoot

p

i

m
a
c

### l2 l1 l3

### p4 p3 p2

p
1

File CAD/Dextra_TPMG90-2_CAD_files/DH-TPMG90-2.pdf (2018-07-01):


x
z

x0

z0

z0

z0

z0 x | z0 0

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
x | z3 1

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
x2 x2
z2

z2
z2

z2

x3

x3 x3
x3

z3

z3 | z3
z3

rightWrist

p

i

m
a
c

l2 l1 l3

p

4

p

3

p

2

p1

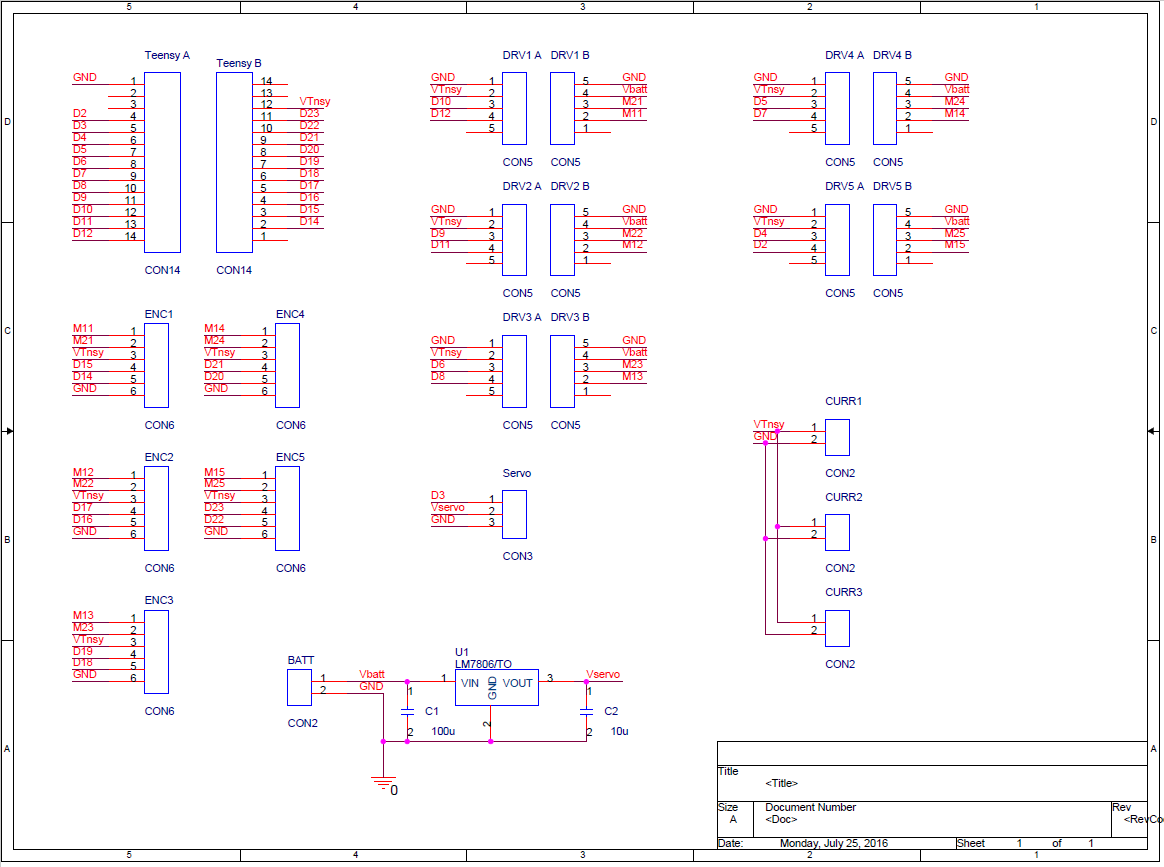
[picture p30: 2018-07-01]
Schematics/DEXTRA_ORIGINAL.png

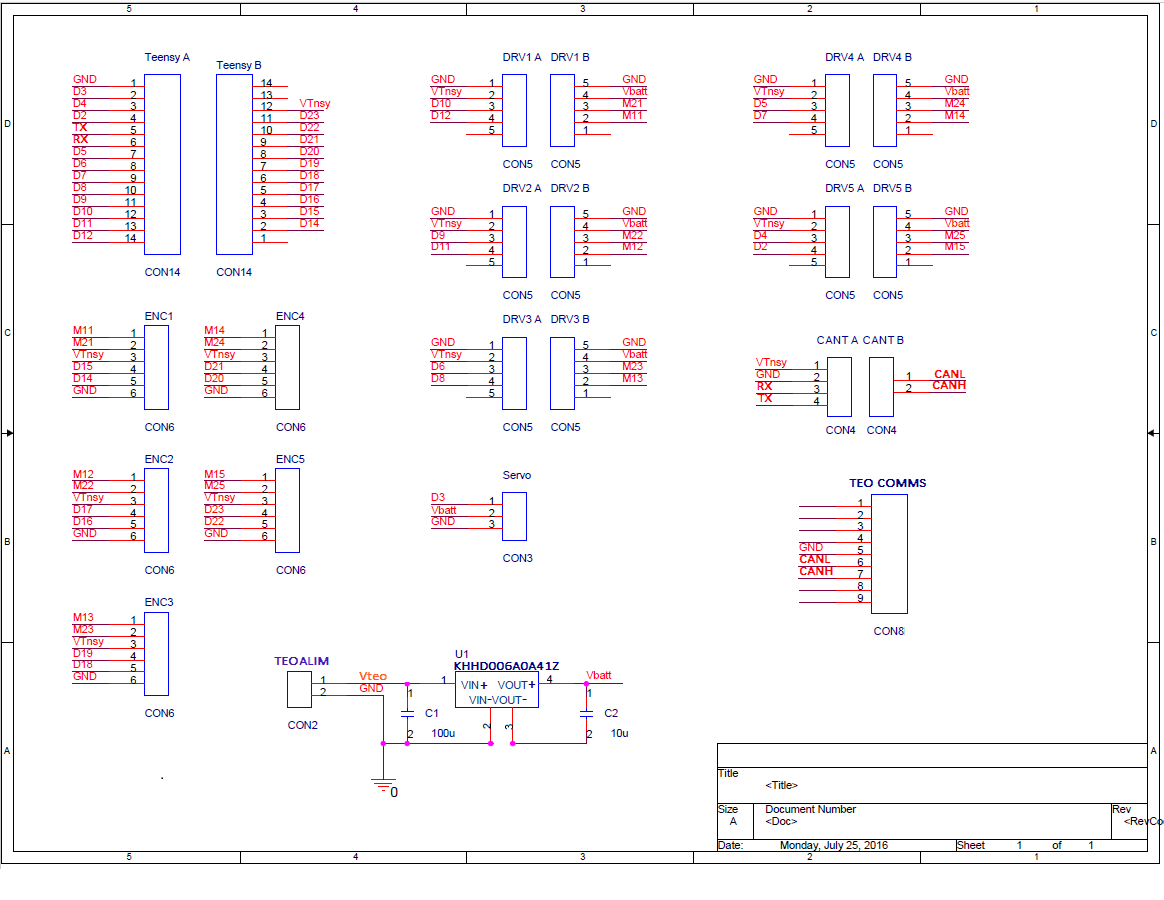
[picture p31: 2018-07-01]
Schematics/DEXTRA_TPMG90-2.png

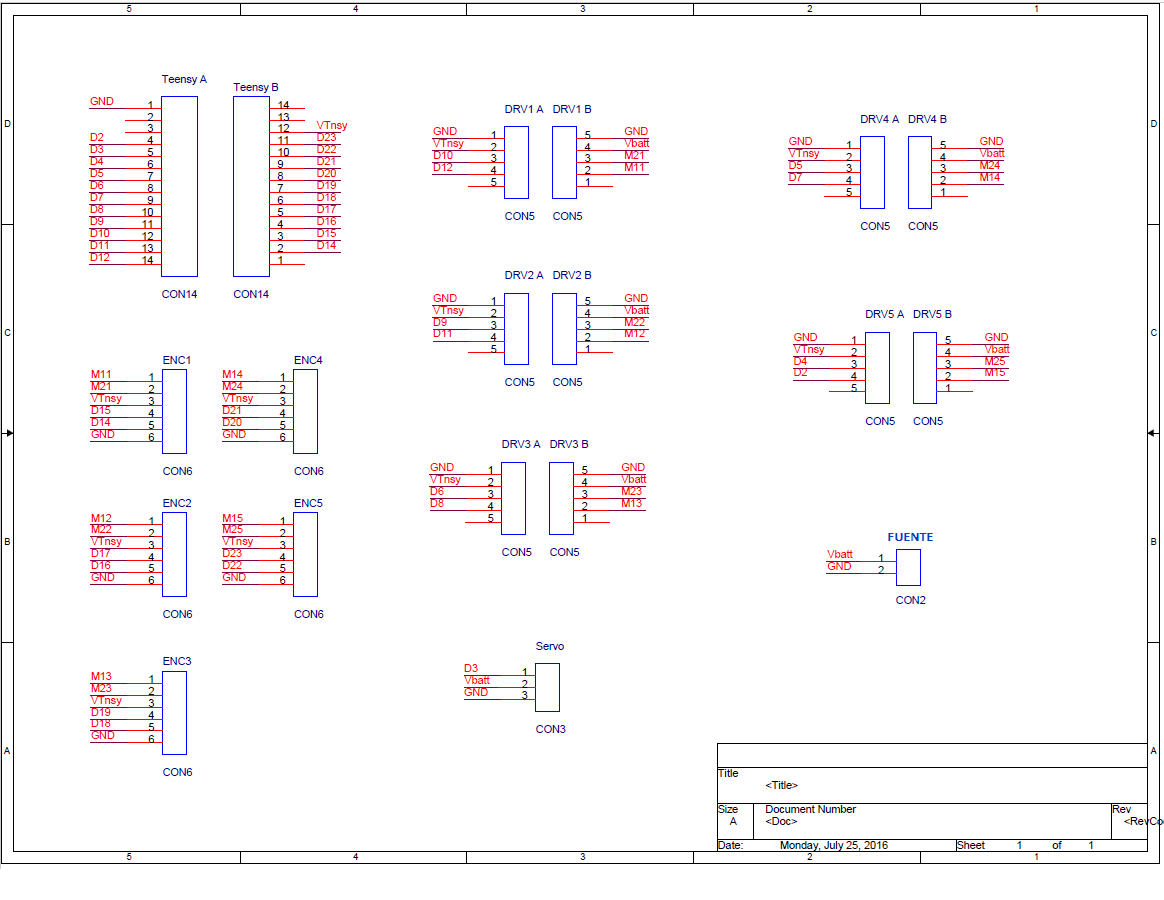
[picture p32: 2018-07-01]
Schematics/DEXTRA_TPMG90-1.png

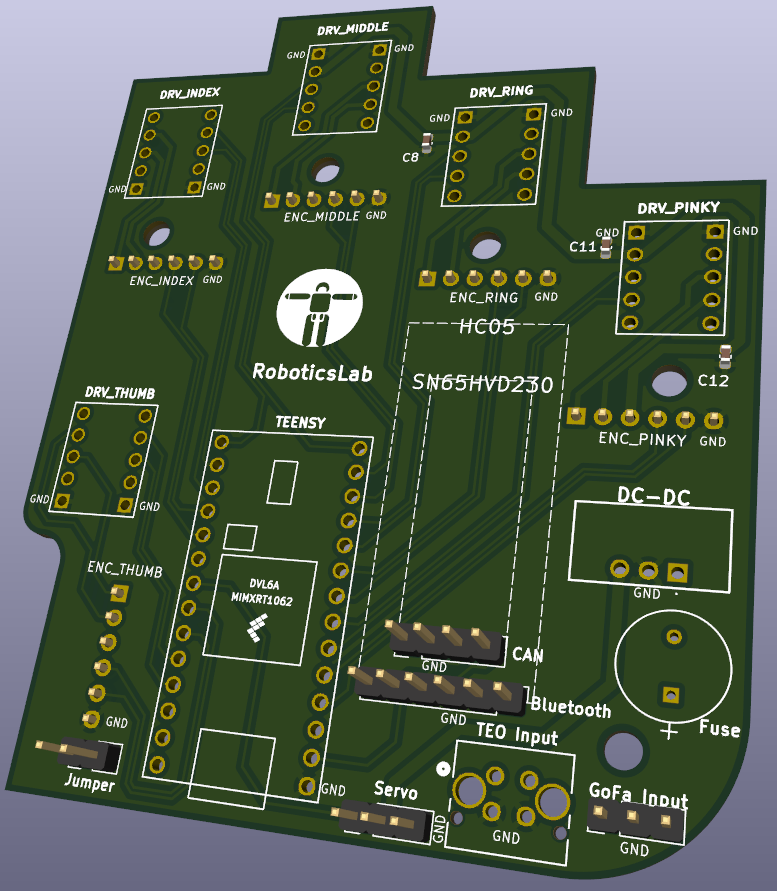
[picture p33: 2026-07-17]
PCB/PCB_DorsalTPMG90S/photos/3d-front.png

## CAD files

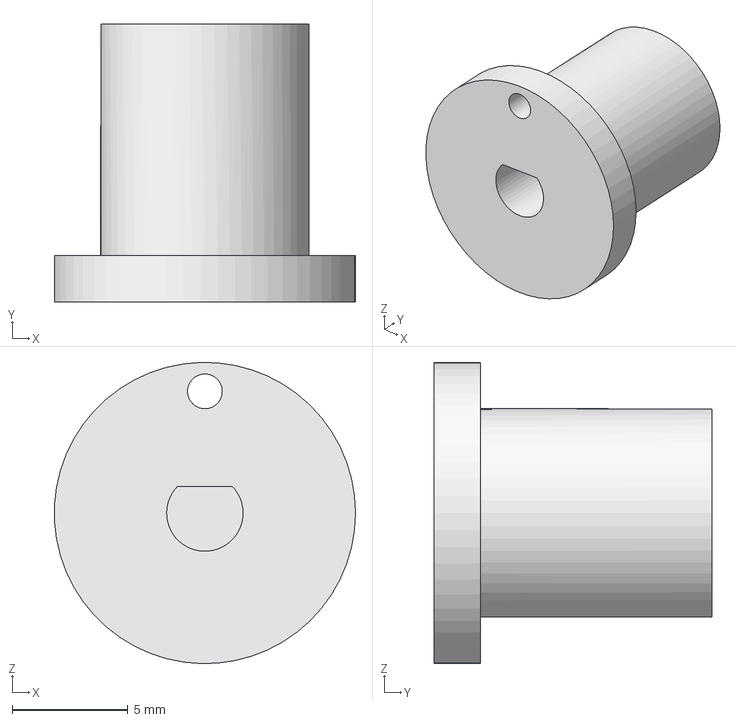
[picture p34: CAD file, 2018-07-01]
CAD/Dextra_ORIGINAL_CAD_files/spool.fcstd
13.0 x 12.0 x 13.0 mm

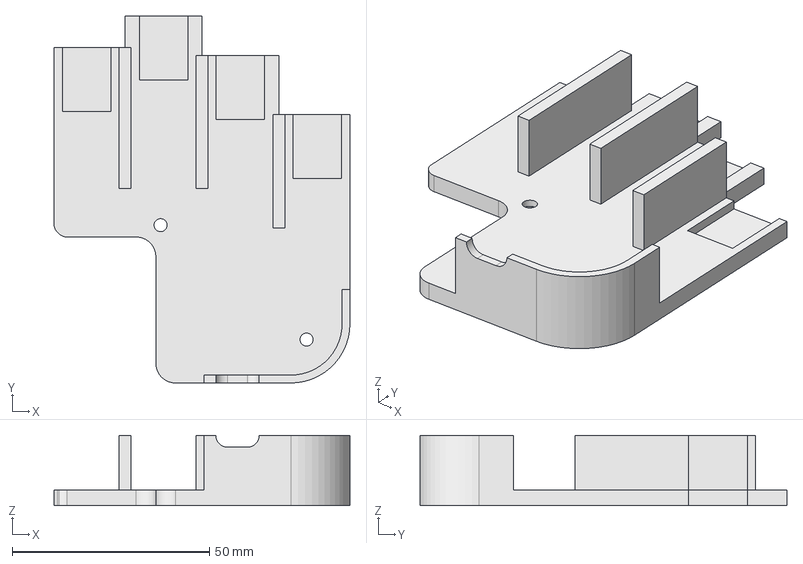
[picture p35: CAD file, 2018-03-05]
CAD/Dextra_TPMG90-1_CAD_files/palmTPMG90-1.fcstd
75.0 x 93.0 x 17.8 mm

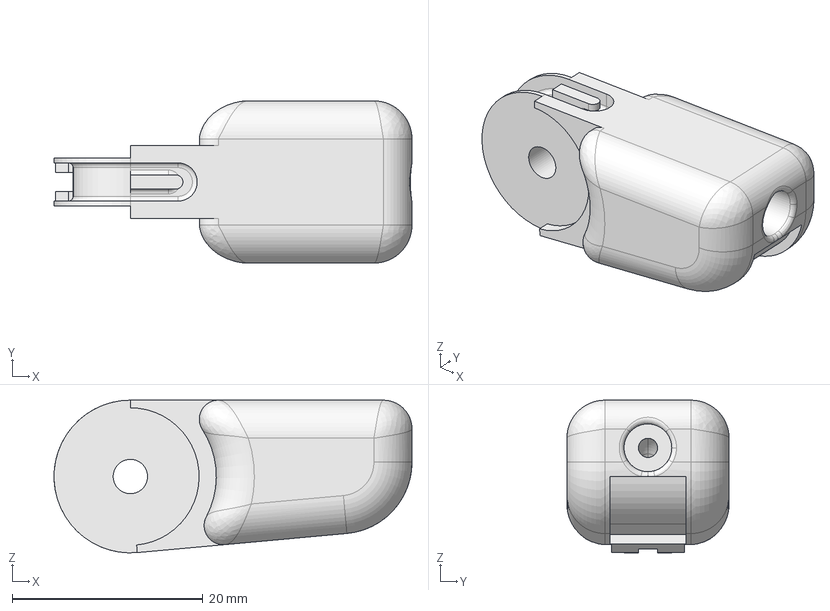
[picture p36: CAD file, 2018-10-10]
CAD/Dextra_TPMG90-2_CAD_files/distal_tumbTPMG90-2.FCStd
37.5 x 17.0 x 16.0 mm

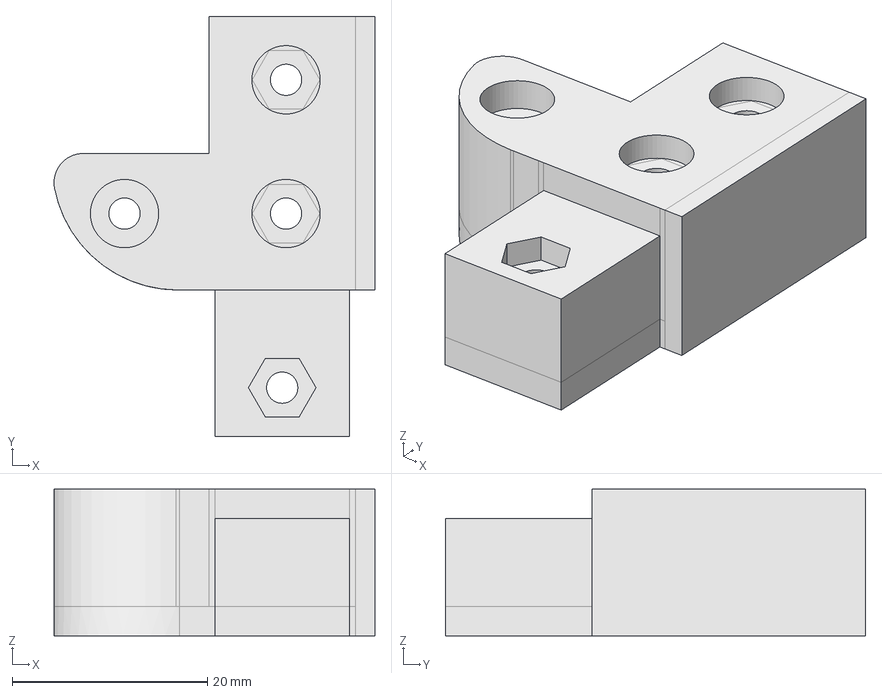
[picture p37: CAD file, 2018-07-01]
CAD/Dextra_TPMG90-2_CAD_files/Left_hand/LEFTwristadapterTPMG90-2.FCStd
32.9 x 43.0 x 15.0 mm

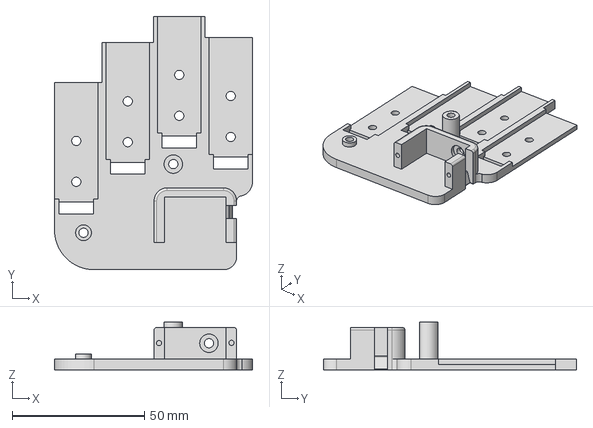
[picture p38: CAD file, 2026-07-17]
CAD/Dextra_TPMG90S_CAD_files/step/dorsal-right.step
75.0 x 96.0 x 18.0 mm

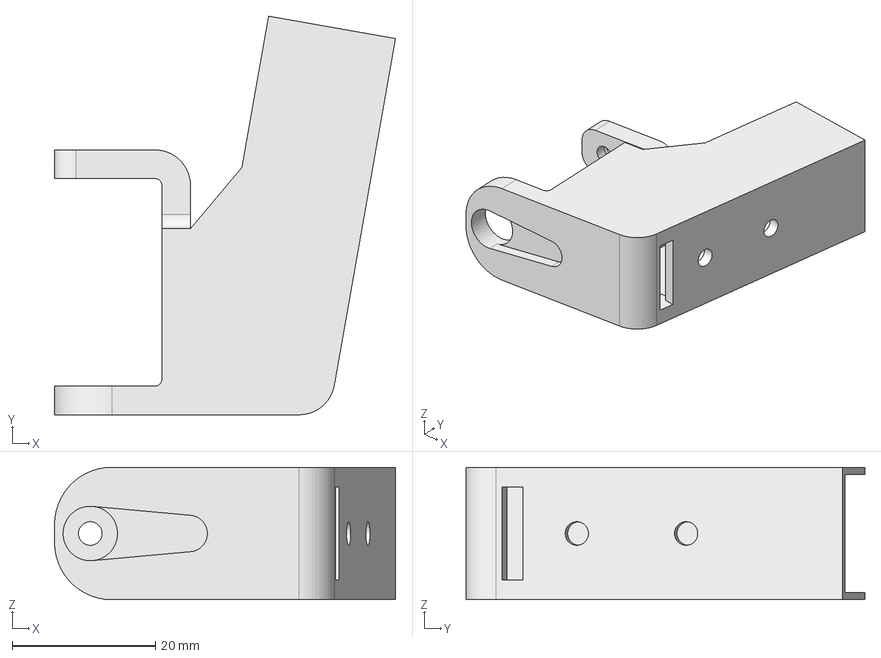
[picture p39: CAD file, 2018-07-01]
CAD/Dextra_ORIGINAL_CAD_files/abductor.fcstd
47.6 x 55.7 x 18.5 mm

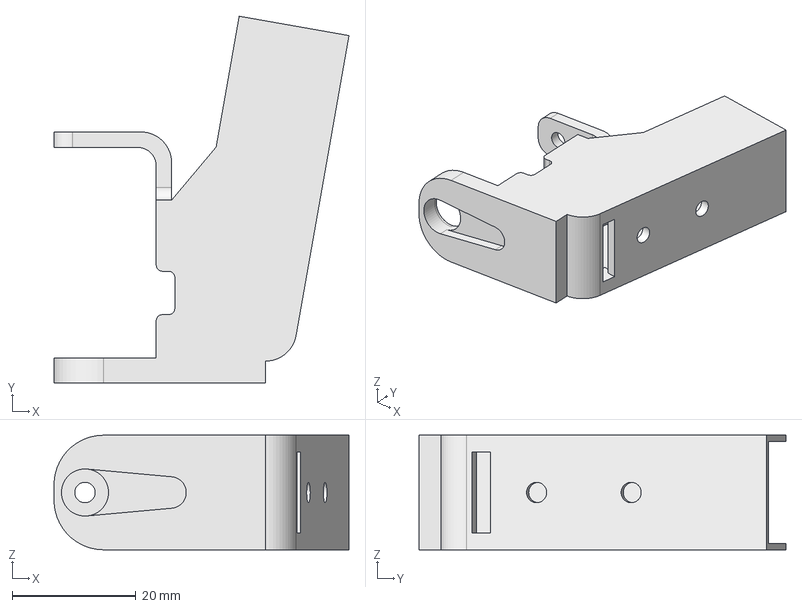
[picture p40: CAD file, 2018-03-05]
CAD/Dextra_TPMG90-1_CAD_files/abductorTPMG90-1.FCStd
47.6 x 59.2 x 18.5 mm

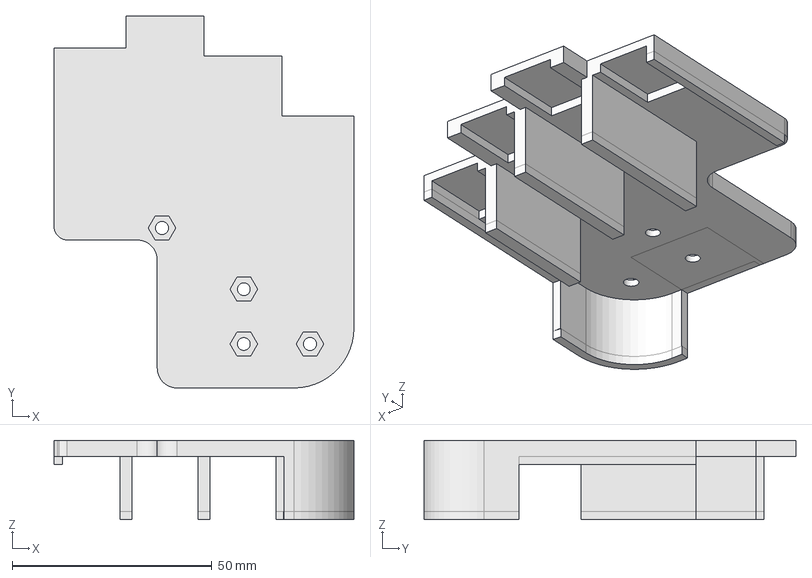
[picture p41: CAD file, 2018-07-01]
CAD/Dextra_TPMG90-2_CAD_files/Left_hand/LEFTpalmTPMG90-2.FCStd
75.0 x 93.0 x 19.8 mm

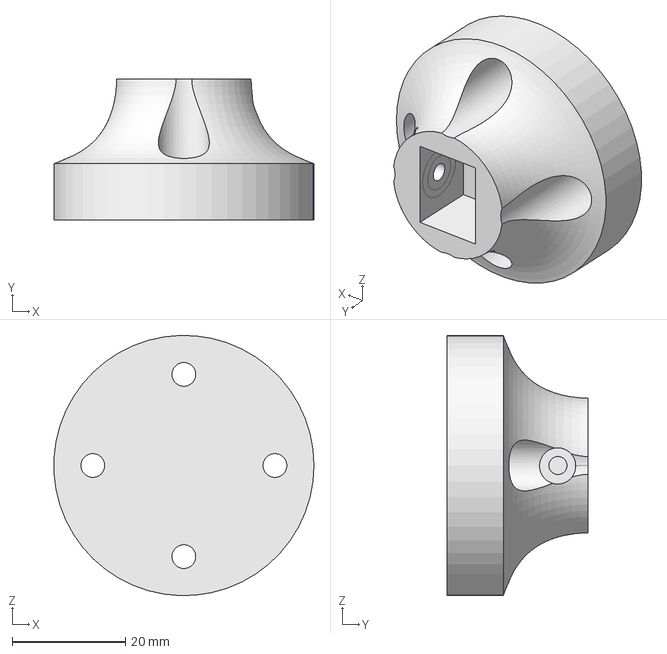
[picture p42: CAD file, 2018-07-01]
CAD/Dextra_TPMG90-2_CAD_files/wristTPMG90-2.FCStd
46.0 x 25.0 x 46.0 mm

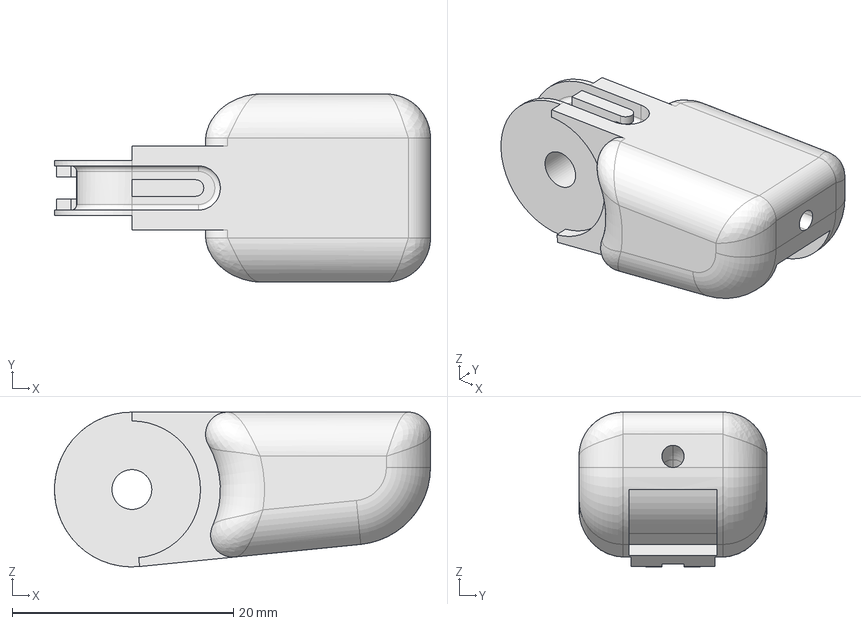
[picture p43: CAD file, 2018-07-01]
CAD/Dextra_ORIGINAL_CAD_files/distal.fcstd
34.0 x 17.0 x 14.0 mm

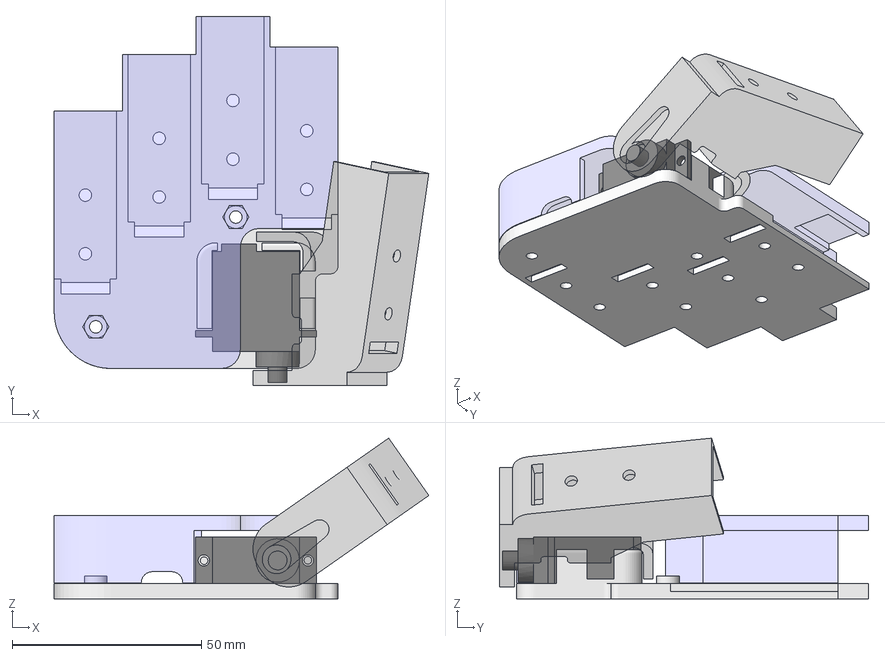
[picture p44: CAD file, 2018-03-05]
CAD/Dextra_TPMG90-1_CAD_files/dorsalTPMG90-1.FCStd
99.0 x 97.5 x 42.5 mm
servo
abbbb
palm

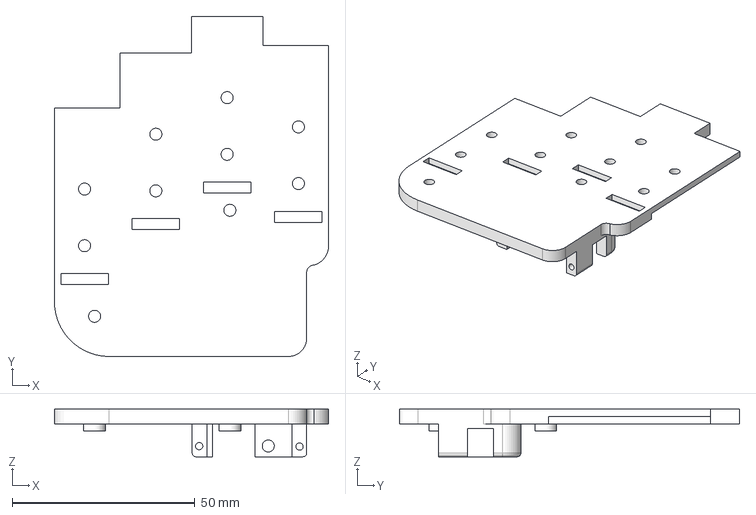
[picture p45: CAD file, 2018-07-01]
CAD/Dextra_TPMG90-2_CAD_files/Left_hand/LEFTdorsalTPMG90-2.FCStd
75.0 x 93.0 x 13.0 mm

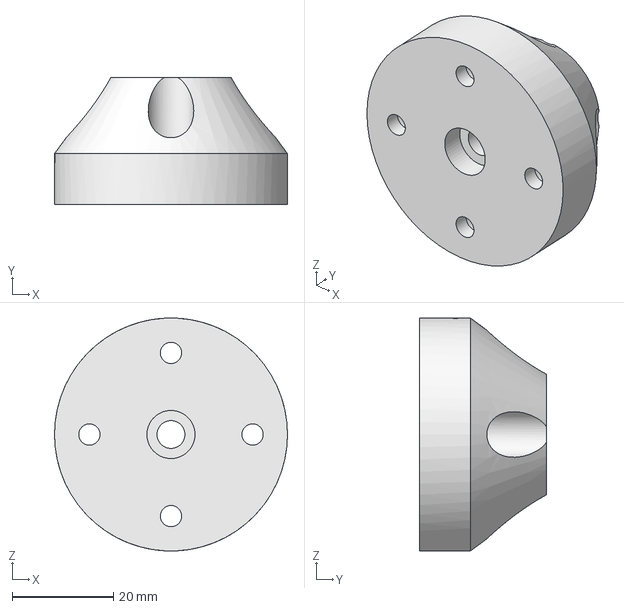
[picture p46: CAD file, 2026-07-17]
CAD/Dextra_TPMG90S_CAD_files/step/wrist-teo.step
46.0 x 25.0 x 46.0 mm

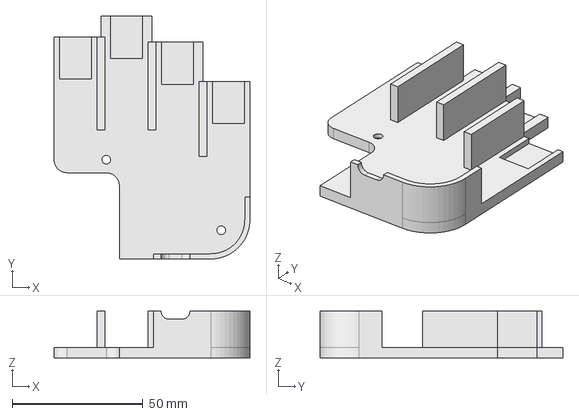
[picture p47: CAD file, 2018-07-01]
CAD/Dextra_ORIGINAL_CAD_files/palm.fcstd
75.0 x 93.0 x 17.8 mm

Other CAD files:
CAD/Dextra_TPMG90S_CAD_files/step/dorsal-left.step
CAD/Dextra_TPMG90-2_CAD_files/palmTPMG90-2.FCStd
CAD/Dextra_TPMG90-1_CAD_files/towerproservo.FCStd
CAD/Dextra_TPMG90-2_CAD_files/wristadapterTPMG90-2.FCStd
CAD/Dextra_ORIGINAL_CAD_files/distal_thumb.fcstd
CAD/Dextra_ORIGINAL_CAD_files/dorsal.fcstd
CAD/Dextra_ORIGINAL_CAD_files/middle.fcstd
CAD/Dextra_ORIGINAL_CAD_files/motor_holder.fcstd
CAD/Dextra_ORIGINAL_CAD_files/motor_holder_thumb.fcstd
CAD/Dextra_ORIGINAL_CAD_files/proximal.fcstd
CAD/Dextra_ORIGINAL_CAD_files/proximal_thumb.fcstd
CAD/Dextra_TPMG90-1_CAD_files/abductorTPMG90-1.stl
CAD/Dextra_TPMG90-1_CAD_files/dorsalTPMG90-1.stl
CAD/Dextra_TPMG90-1_CAD_files/palmTPMG90-1.stl
CAD/Dextra_TPMG90-1_CAD_files/towerproservo.stl
CAD/Dextra_TPMG90-2_CAD_files/distalTPMG90-2.FCStd
CAD/Dextra_TPMG90-2_CAD_files/dorsalTPMG90-2.FCStd
CAD/Dextra_TPMG90S_CAD_files/3mf/abductor.3mf
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

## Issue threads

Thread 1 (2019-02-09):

PCB design considerations

jgagom, 2019-02-09:
Ideas to design a PCB layout

jgagom, 2019-02-09:
Regarding PCB traces:

- 45° angles shorten the electrical path between components.
- High speed logic signals (above 200 MHz) can get reflected off the back of the angle, causing interference.
- 90º has the likelihood of being etched narrower than your standard trace width.
- 90º traces back might not be fully etched, thay could cause shorts.

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

andreagil, 2019-02-09:
Steps from breadboard --> to PCB board.

PCB design:
- Schematics design (using KiCad)
- PCB design (routing, components and PCB dimensions)
- BOM list (Bill of materials): actual components to be used (in case connectors of any type have to be considered: USB, expansion jumper connectors...)

SCHEMATICS
It is assumed that each connector is a box with inputs and output. The schematics are the conections between the pins of that boxes without considering the dimensions of any component or the final design of the final PCB (simply the connections, without taking into account the size of hardware).

It is needed:

- **The datasheet** (connections) and **CAD files** (dimensions) from each component (drivers) and the central processor. I assume  drivers are bought (not included in the PCB), but the datasheet is needed to match each output (10 outputs from the photo I have seen).
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

PCB DESIGN
It is needed:

- The schematic.

- **Type of connector**. Doubt: Do I have to take into account connectors? In case the answer is yes, what type of expansion jumper connector are required: SMD (Surface Mounted Device) or through hole connectors?

(Connectors are required in case there are electronic elemens under the drivers which cannot be touching the PCB. These connectors are used as spacers)

So, final doubt: do you want to maintain the black connectors (below image) between the breadboard and the drivers and central processor? or do you want to weld the drivers directly in the PCB holes? (This issue can be considered in the PCB printing process, the process can take into account the black connector or not)

Current black connectors:
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

Additionaly, the connections which are going to be ignored are flagged in the next figure
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

jgagom, 2019-02-09:
Regarding datasheets:

- DRV8838 Single Brushed DC Motor Driver Carrier
https://www.pololu.com/product/2990

- Microcontroller: Teensy 3.2
https://www.pjrc.com/store/teensy32.html

- Servo TowerPro MG90 (directly connected to the PCB):
https://servodatabase.com/servo/towerpro/mg90

Regarding CAD files (use right hand ones):

- https://github.com/jgagom/Dextra/tree/dextraTPMG90/Dextra_TPMG90-2_CAD_files

Important [!] - Electronic components won't be welded to the PCB.
Solution: **holes for through-hole components** (check image bellow) for straight 0.1 inch (2.54 mm) spacing (male-male).

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

PeterBowman, 2019-06-20:
The design was successfully validated: https://github.com/roboticslab-uc3m/Dextra/issues/5. Can we close this?

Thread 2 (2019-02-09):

CAN-Bus implementation  - SN65HVD230 CAN Transceiver

jgagom, 2019-02-09:
SN65HVD230 CAN Board

https://www.waveshare.com/wiki/SN65HVD230_CAN_Board

PeterBowman, 2019-06-14:
CAN master (YARP side) software implementation: https://github.com/roboticslab-uc3m/yarp-devices/issues/176.

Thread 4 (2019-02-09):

KiCad Dorsal Design

andreagil, 2019-02-09:
Steps from breadboard --> to PCB board.

PCB design:
- Schematics design (using KiCad)
- PCB design (routing, components and PCB dimensions)
- BOM list (Bill of materials): actual components to be used (in case connectors of any type have to be considered: USB, expansion jumper connectors...)

SCHEMATICS
It is assumed that each connector is a box with inputs and output. The schematics are the conections between the pins of that boxes without considering the dimensions of any component or the final design of the final PCB (simply the connections, without taking into account the size of hardware).

It is needed:

- **The datasheet** (connections) and **CAD files** (dimensions) from each component (drivers) and the central processor. I assume  drivers are bought (not included in the PCB), but the datasheet is needed to match each output (10 outputs from the photo I have seen).
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

PCB DESIGN
It is needed:

- The schematic.

- **Type of connector**. Doubt: Do I have to take into account connectors? In case the answer is yes, what type of expansion jumper connector are required: SMD (Surface Mounted Device) or through hole connectors?

(Connectors are required in case there are electronic elemens under the drivers which cannot be touching the PCB. These connectors are used as spacers)

So, final doubt: do you want to maintain the black connectors (below image) between the breadboard and the drivers and central processor? or do you want to weld the drivers directly in the PCB holes? (This issue can be considered in the PCB printing process, the process can take into account the black connector or not)

Current black connectors:
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

Additionaly, the connections which are going to be ignored are flagged in the next figure
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

Closed 2019-02-09.

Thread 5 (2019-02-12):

Schematics Design

andreagil, 2019-02-12:
In order to design the schematics, only the connections are taken into account.

It is assumed that each connector is a box with inputs and output. The schematics are the conections between the pins of that boxes without considering the dimensions of any component or the final design of the final PCB (simply the connections, without taking into account the size of hardware).

Steps:

1) Create connectors for each driver, encoder and for the Teensy following the datasheet information of the pines. The correct orientation is not needed at this stage. (In the schematics presented below, components in the PCB should be rotated 180 º.)
Components connections have been created following the pin information of the spreadsheet:
In the case of the drivers:
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
In the case of the microcontroller:
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

2) Add the labels to each pin so that KiCad is able to understand each connection among the electronic components.

3) Put an X where there is no connection.

4) Annotate the component. (designator ? is automatically changed by a number)

Final result:
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
Comment: the name of the labels in a schematic usually corresponds to the functionality of each pin. In this case, for simplicity (and because I'm not quite sure of which are the funcionalities of the left pins of the microcontroller), the name of the PINS: PIN0, PIN1... have been used.

Additional material used for the creation of the schematics:
https://www.youtube.com/watch?v=zK3rDhJqMu0

jgvictores, 2019-03-27:
Pending: remove via from design

jgvictores, 2019-04-10:
Pending: join PCBs (divide by row to allow cutting, such as holes for a row of pins)

jgvictores, 2019-04-12:
> Pending: join PCBs (divide by row to allow cutting, such as holes for a row of pins)

Perhaps manufacturers can do this for us. We'll find out!

PeterBowman, 2019-06-14:
This design has been validated today on our new right hand PCB. A firmware update is required due to a small change in the Teensy's pinout, see https://github.com/PeterBowman/Dextra/commit/e3cab0e060824f9b8a36afa21fc96b95bcb19211. To be merged soon.

TODO list targeted at future iterations:

* Reverse the Pololu connector pinout, i.e. bring the ground pin back to the left side (so that wires need not to be flipped on their way from the board to the Pololus).
* There are several screw holes, we just need two (top-left and bottom-right). Removing them would leave more room for the CAN transceiver (https://github.com/jgagom/Dextra/issues/2) and the DC/DC converter (https://github.com/jgagom/Dextra/issues/3).

PeterBowman, 2019-06-20:
Merged into default branch at https://github.com/roboticslab-uc3m/Dextra/commit/cc3cdb3ec0158abe4dacd742bfecd29fd41c0f4c. The obsolete right-hand design was removed (still accessible through commit history).

Closed 2019-06-20.

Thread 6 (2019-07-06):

Fingers behave oddly when commanded to 15.9

PeterBowman, 2019-07-06:
First observed at https://github.com/roboticslab-uc3m/sign-language-papers/issues/7#issuecomment-460450706 (private repo). If any finger is commanded to achieve 15.9, it starts spinning without seemingly aiming for a reachable pose.

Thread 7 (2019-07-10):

Improvements on Schematics Design

jgvictores, 2019-07-10:
From https://github.com/roboticslab-uc3m/Dextra/issues/5#issuecomment-502228968

* Reverse the Pololu connector pinout, i.e. bring the ground pin back to the left side (so that wires need not to be flipped on their way from the board to the Pololus).
* There are several screw holes, we just need two (top-left and bottom-right). Removing them would leave more room for the CAN transceiver (https://github.com/roboticslab-uc3m/Dextra/issues/2) and the DC/DC converter (https://github.com/roboticslab-uc3m/Dextra/issues/3).

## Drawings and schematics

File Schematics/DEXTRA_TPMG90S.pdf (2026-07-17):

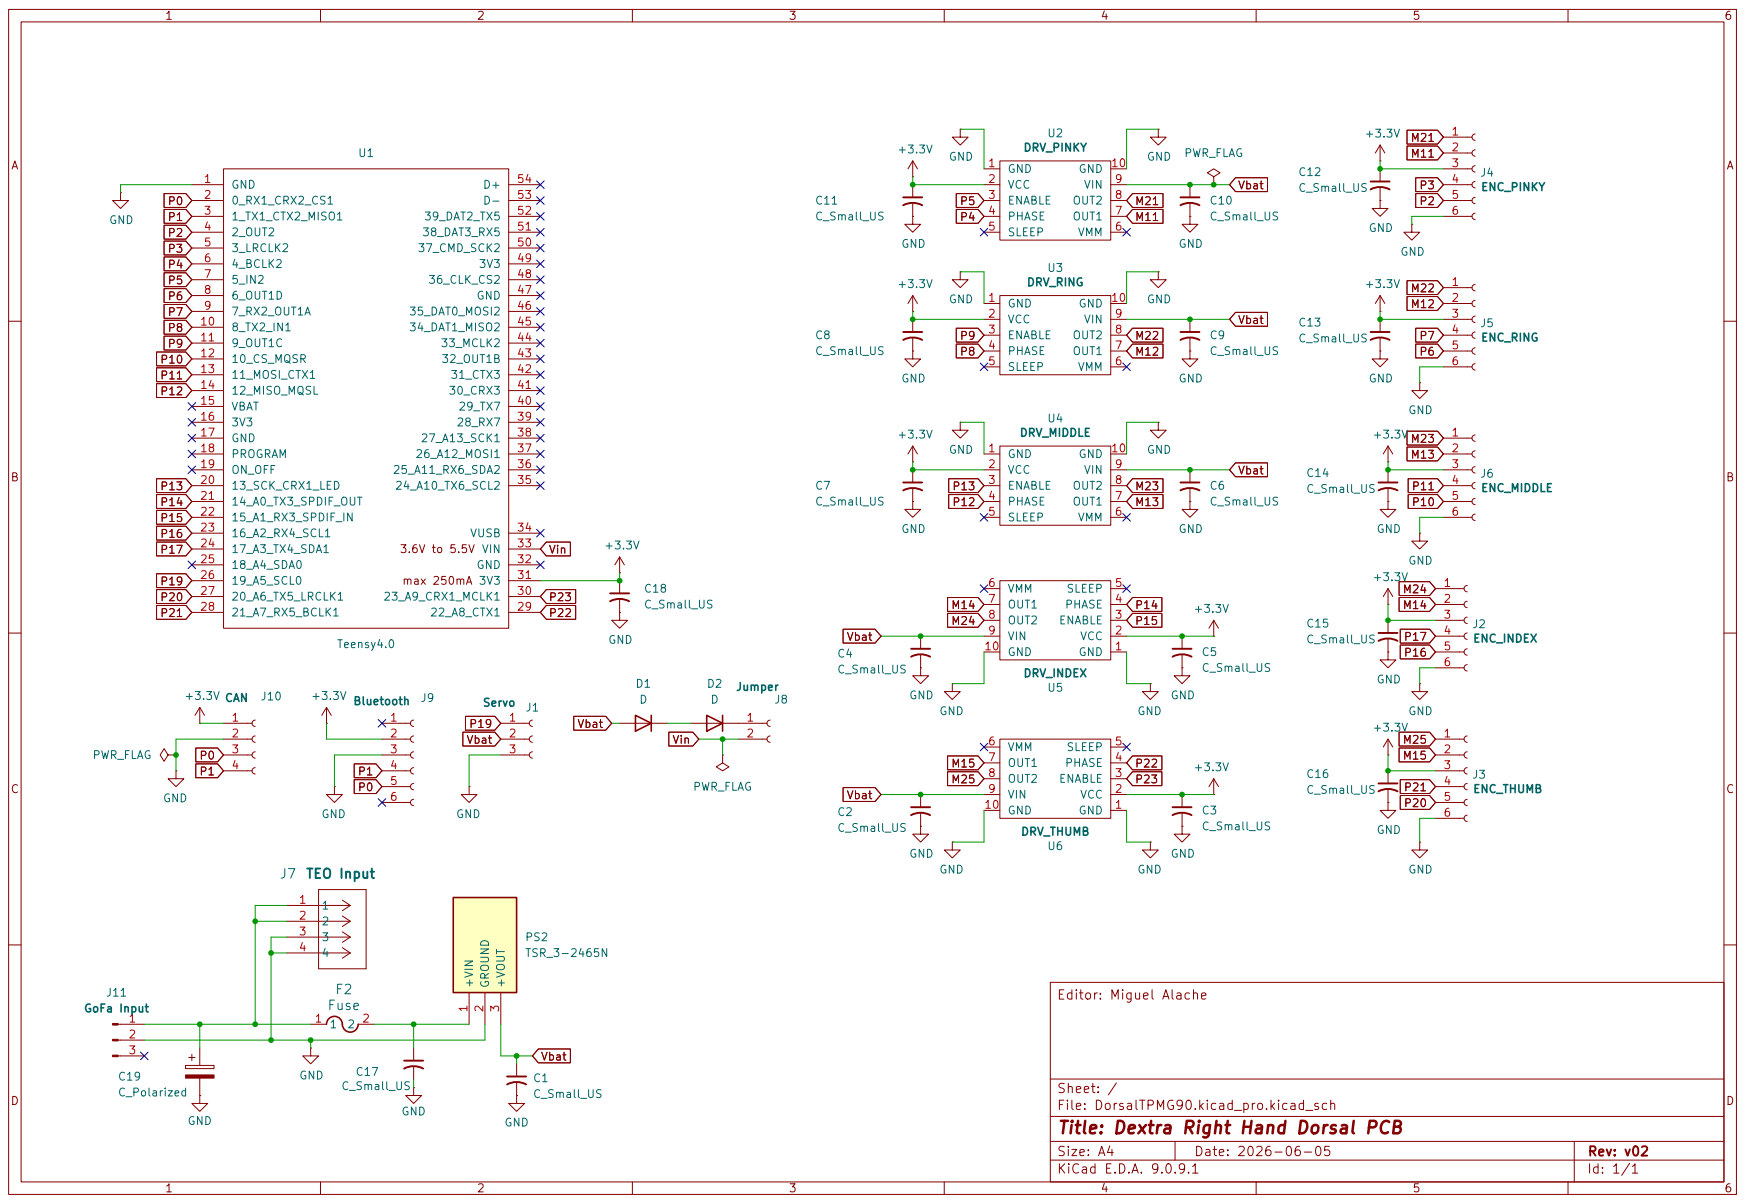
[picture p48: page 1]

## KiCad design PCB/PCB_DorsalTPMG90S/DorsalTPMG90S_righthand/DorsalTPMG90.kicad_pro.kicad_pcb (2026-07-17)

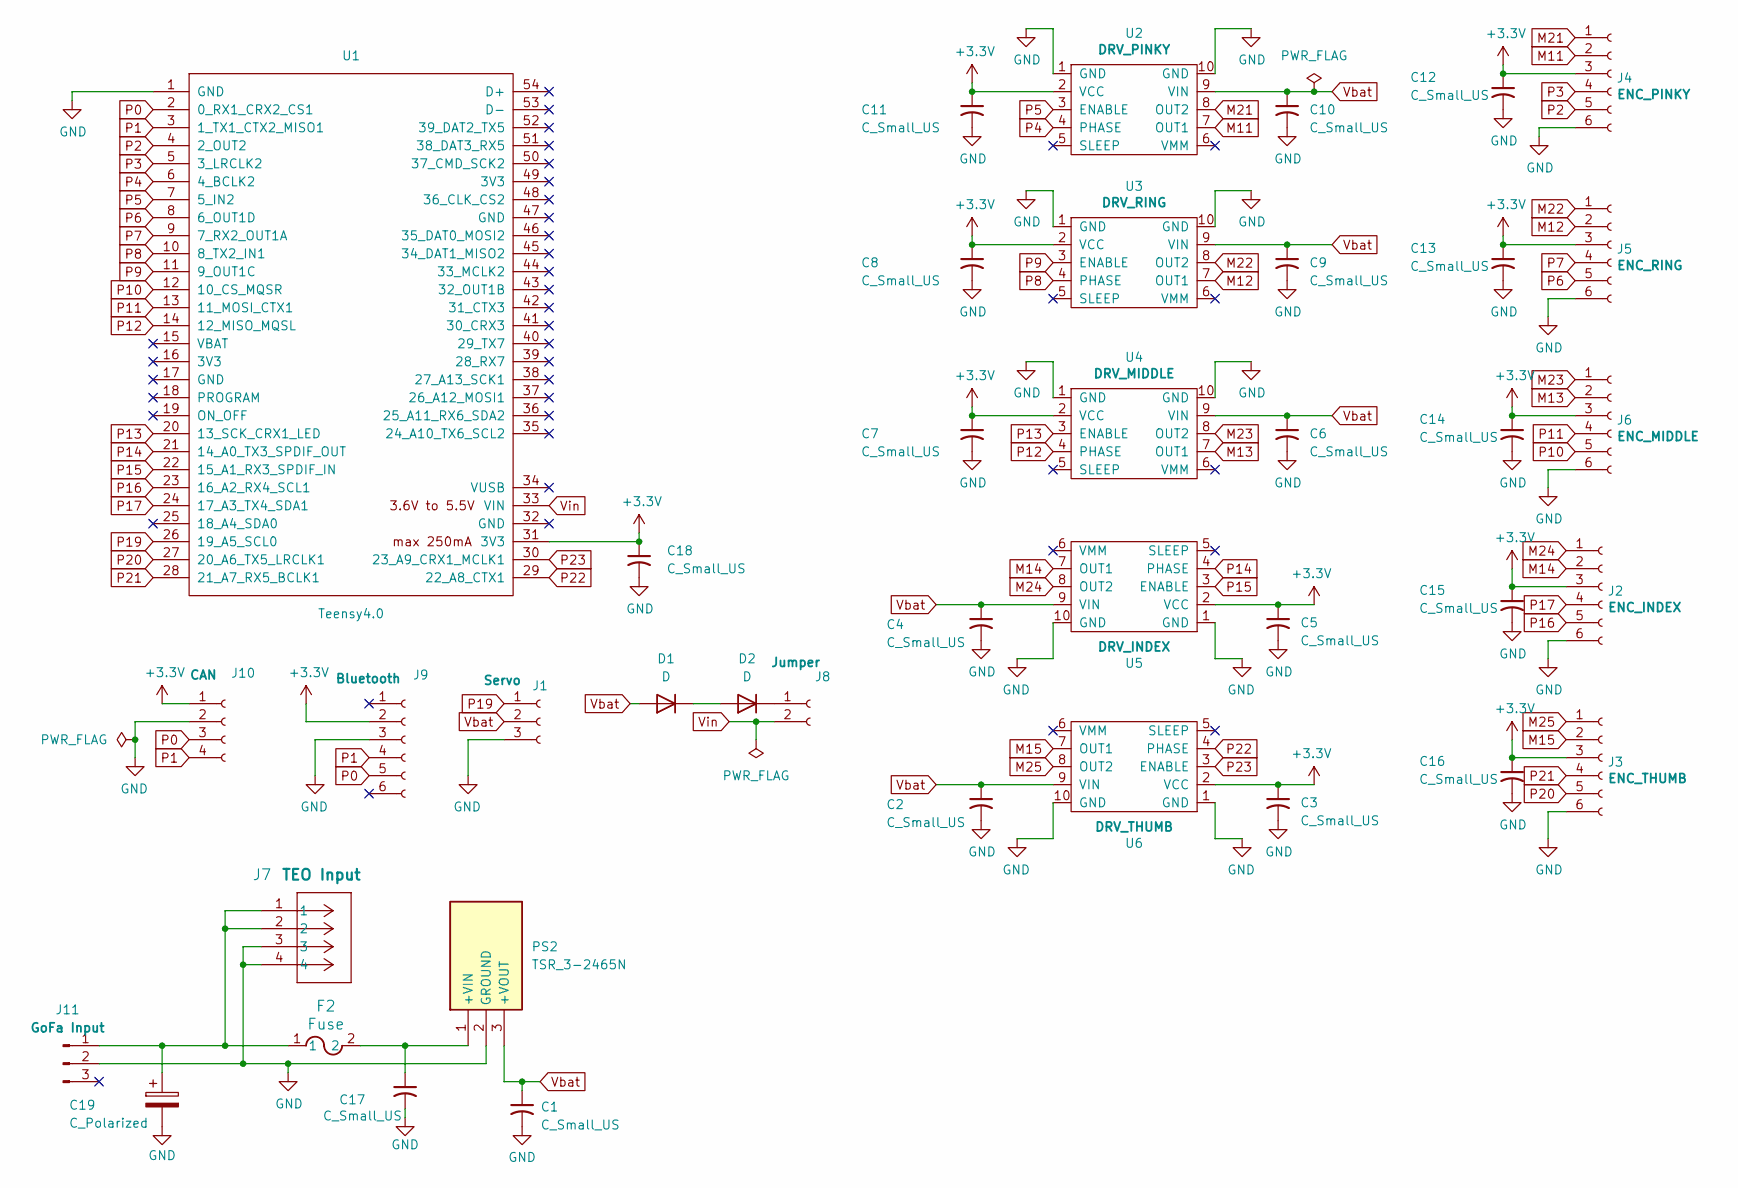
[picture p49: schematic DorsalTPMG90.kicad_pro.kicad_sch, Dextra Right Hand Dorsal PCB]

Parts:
C1, C2, C3, C4, C5, C6, C7, C8, C9, C10, C11, C12, C13, C14, C15, C16, C18: C_Small_US; C_0603_1608Metric
C17: C_Small_US; C_0805_2012Metric
C19: C_Polarized; Cin
D1, D2: D; D_SOD-123
F2: Fuse; FUSE_560_1009_LTF
J1: Servo; PinHeader_1x03_P2.54mm_Vertical
J2: ENC_INDEX; PinHeader_1x06_P2.54mm_Vertical
J3: ENC_THUMB; PinHeader_1x06_P2.54mm_Vertical
J4: ENC_PINKY; PinHeader_1x06_P2.54mm_Vertical
J5: ENC_RING; PinHeader_1x06_P2.54mm_Vertical
J6: ENC_MIDDLE; PinHeader_1x06_P2.54mm_Vertical
J7: TEO Input; conector_Molex_2x2
J8: Jumper; PinHeader_1x02_P2.54mm_Vertical
J9: Bluetooth; PinHeader_1x06_P2.54mm_Vertical
J10: CAN; PinHeader_1x04_P2.54mm_Vertical
J11: GoFa Input; PinHeader_1x03_P2.54mm_Vertical
PS2: TSR_3-2465N; TSR32465N; Manufacturer_Part_Number TSR 3-2465N
U1: Teensy4.0; Teensy40_SidesOnly
U2: DRV_PINKY; Pololu_DRV8838
U3: DRV_RING; Pololu_DRV8838
U4: DRV_MIDDLE; Pololu_DRV8838
U5: DRV_INDEX; Pololu_DRV8838
U6: DRV_THUMB; Pololu_DRV8838

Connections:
+3.3V: C3.1, C5.1, C7.1, C8.1, C11.1, C12.1, C13.1, C14.1, C15.1, C16.1, C18.1, J2.3, J3.3, J4.3, J5.3, J6.3, J9.2, J10.1, U1.31 (3V3), U2.2 (VCC), U3.2 (VCC), U4.2 (VCC), U5.2 (VCC), U6.2 (VCC)
GND: C1.2, C2.2, C3.2, C4.2, C5.2, C6.2, C7.2, C8.2, C9.2, C10.2, C11.2, C12.2, C13.2, C14.2, C15.2, C16.2, C17.2, C18.2, C19.2, J1.3, J2.6, J3.6, J4.6, J5.6, J6.6, J7.3, J7.4, J9.3, J10.2, J11.2, PS2.2 (GROUND), U1.1 (GND), U2.1 (GND), U2.10 (GND), U3.1 (GND), U3.10 (GND), U4.1 (GND), U4.10 (GND), U5.1 (GND), U5.10 (GND), U6.1 (GND), U6.10 (GND)
M11: J4.2, U2.7 (OUT1)
M12: J5.2, U3.7 (OUT1)
M13: J6.2, U4.7 (OUT1)
M14: J2.2, U5.7 (OUT1)
M15: J3.2, U6.7 (OUT1)
M21: J4.1, U2.8 (OUT2)
M22: J5.1, U3.8 (OUT2)
M23: J6.1, U4.8 (OUT2)
M24: J2.1, U5.8 (OUT2)
M25: J3.1, U6.8 (OUT2)
unnamed: D1.1 (K), D2.2 (A)
unnamed: D2.1 (K), J8.1
unnamed: C19.1, F2.1, J7.1, J7.2, J11.1
unnamed: C17.1, F2.2, PS2.1 (+VIN)
P0: J9.5, J10.3, U1.2 (0_RX1_CRX2_CS1)
P1: J9.4, J10.4, U1.3 (1_TX1_CTX2_MISO1)
P2: J4.5, U1.4 (2_OUT2)
P3: J4.4, U1.5 (3_LRCLK2)
P4: U1.6 (4_BCLK2), U2.4 (PHASE)
P5: U1.7 (5_IN2), U2.3 (ENABLE)
P6: J5.5, U1.8 (6_OUT1D)
P7: J5.4, U1.9 (7_RX2_OUT1A)
P8: U1.10 (8_TX2_IN1), U3.4 (PHASE)
P9: U1.11 (9_OUT1C), U3.3 (ENABLE)
P10: J6.5, U1.12 (10_CS_MQSR)
P11: J6.4, U1.13 (11_MOSI_CTX1)
P12: U1.14 (12_MISO_MQSL), U4.4 (PHASE)
P13: U1.20 (13_SCK_CRX1_LED), U4.3 (ENABLE)
P14: U1.21 (14_A0_TX3_SPDIF_OUT), U5.4 (PHASE)
P15: U1.22 (15_A1_RX3_SPDIF_IN), U5.3 (ENABLE)
P16: J2.5, U1.23 (16_A2_RX4_SCL1)
P17: J2.4, U1.24 (17_A3_TX4_SDA1)
P19: J1.1, U1.26 (19_A5_SCL0)
P20: J3.5, U1.27 (20_A6_TX5_LRCLK1)
P21: J3.4, U1.28 (21_A7_RX5_BCLK1)
P22: U1.29 (22_A8_CTX1), U6.4 (PHASE)
P23: U1.30 (23_A9_CRX1_MCLK1), U6.3 (ENABLE)
Vbat: C1.1, C2.1, C4.1, C6.1, C9.1, C10.1, D1.2 (A), J1.2, PS2.3 (+VOUT), U2.9 (VIN), U3.9 (VIN), U4.9 (VIN), U5.9 (VIN), U6.9 (VIN)
Vin: J8.2, U1.33 (VIN)

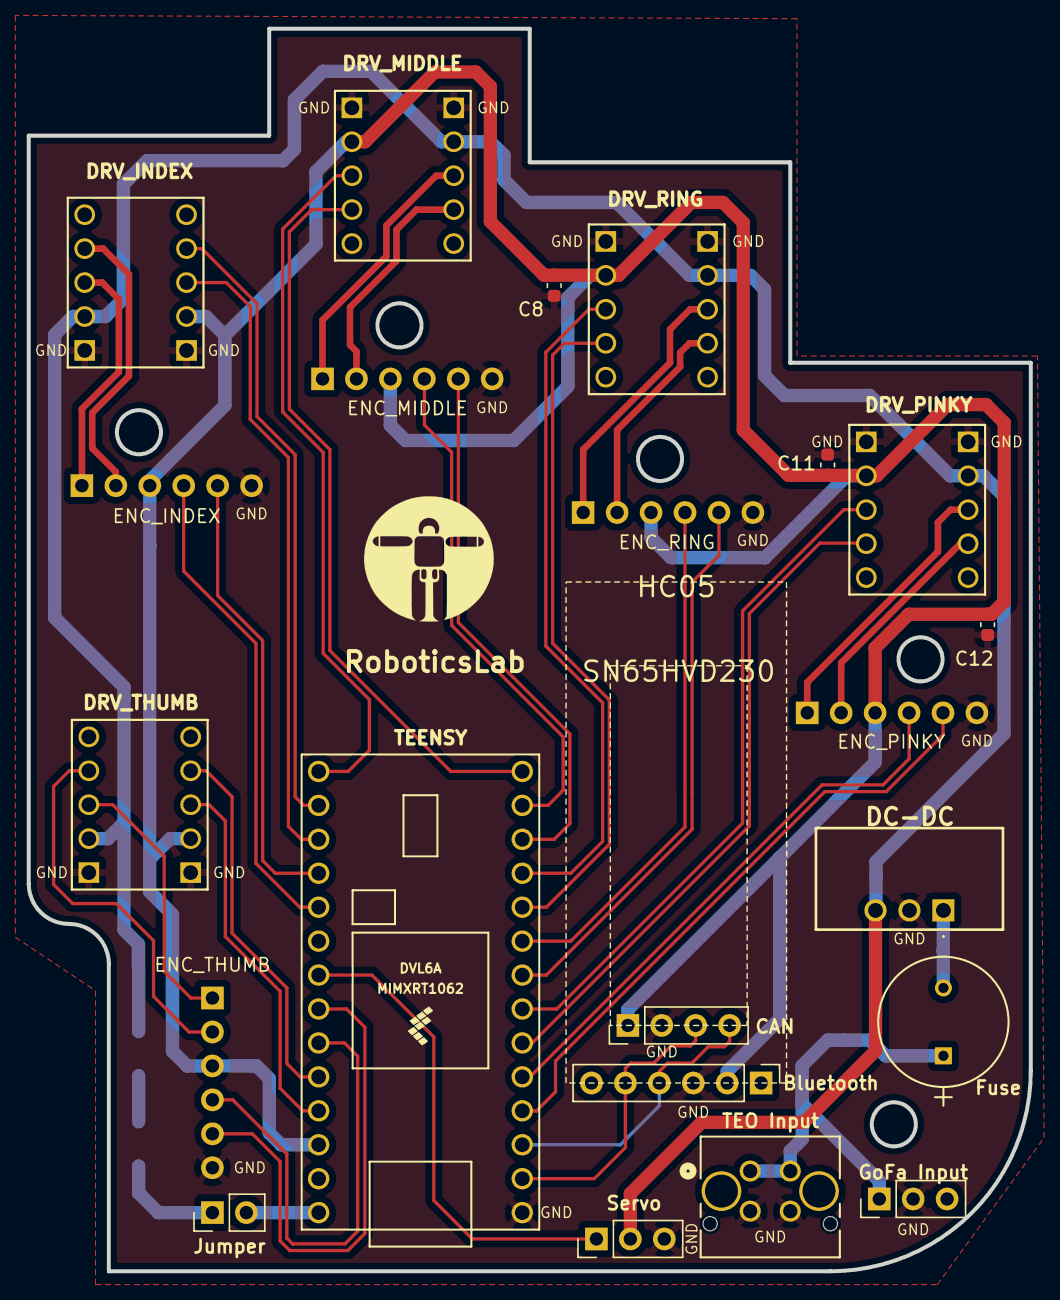
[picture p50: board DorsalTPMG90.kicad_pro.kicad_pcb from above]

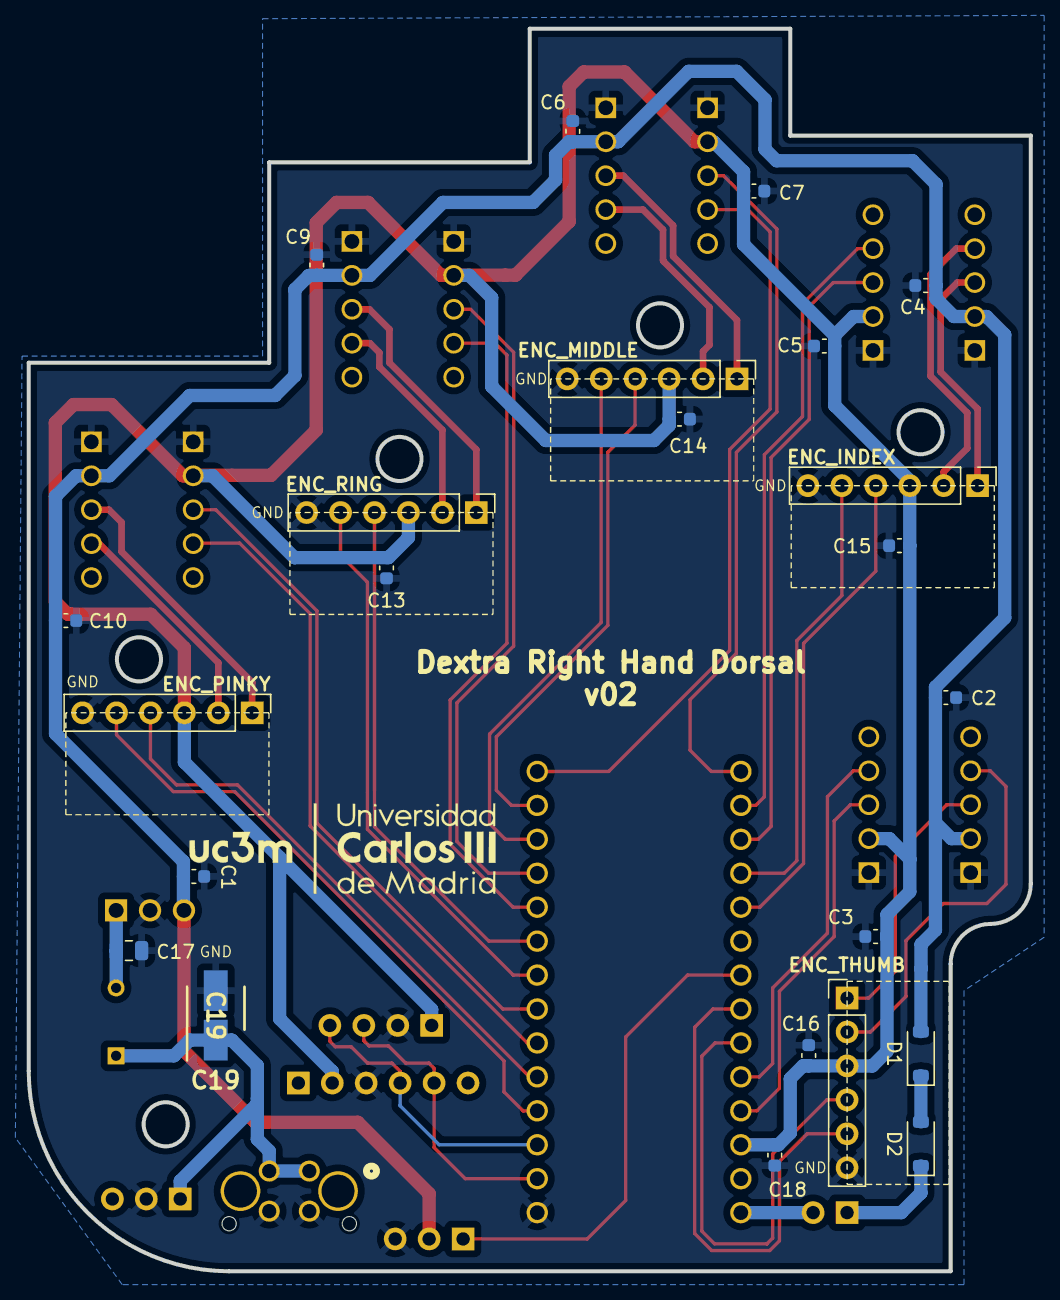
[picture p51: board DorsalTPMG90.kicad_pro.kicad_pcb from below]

Board: 2 copper layers, 75.0 x 93.0 mm, 40 parts (23 on the bottom side), 40 nets.

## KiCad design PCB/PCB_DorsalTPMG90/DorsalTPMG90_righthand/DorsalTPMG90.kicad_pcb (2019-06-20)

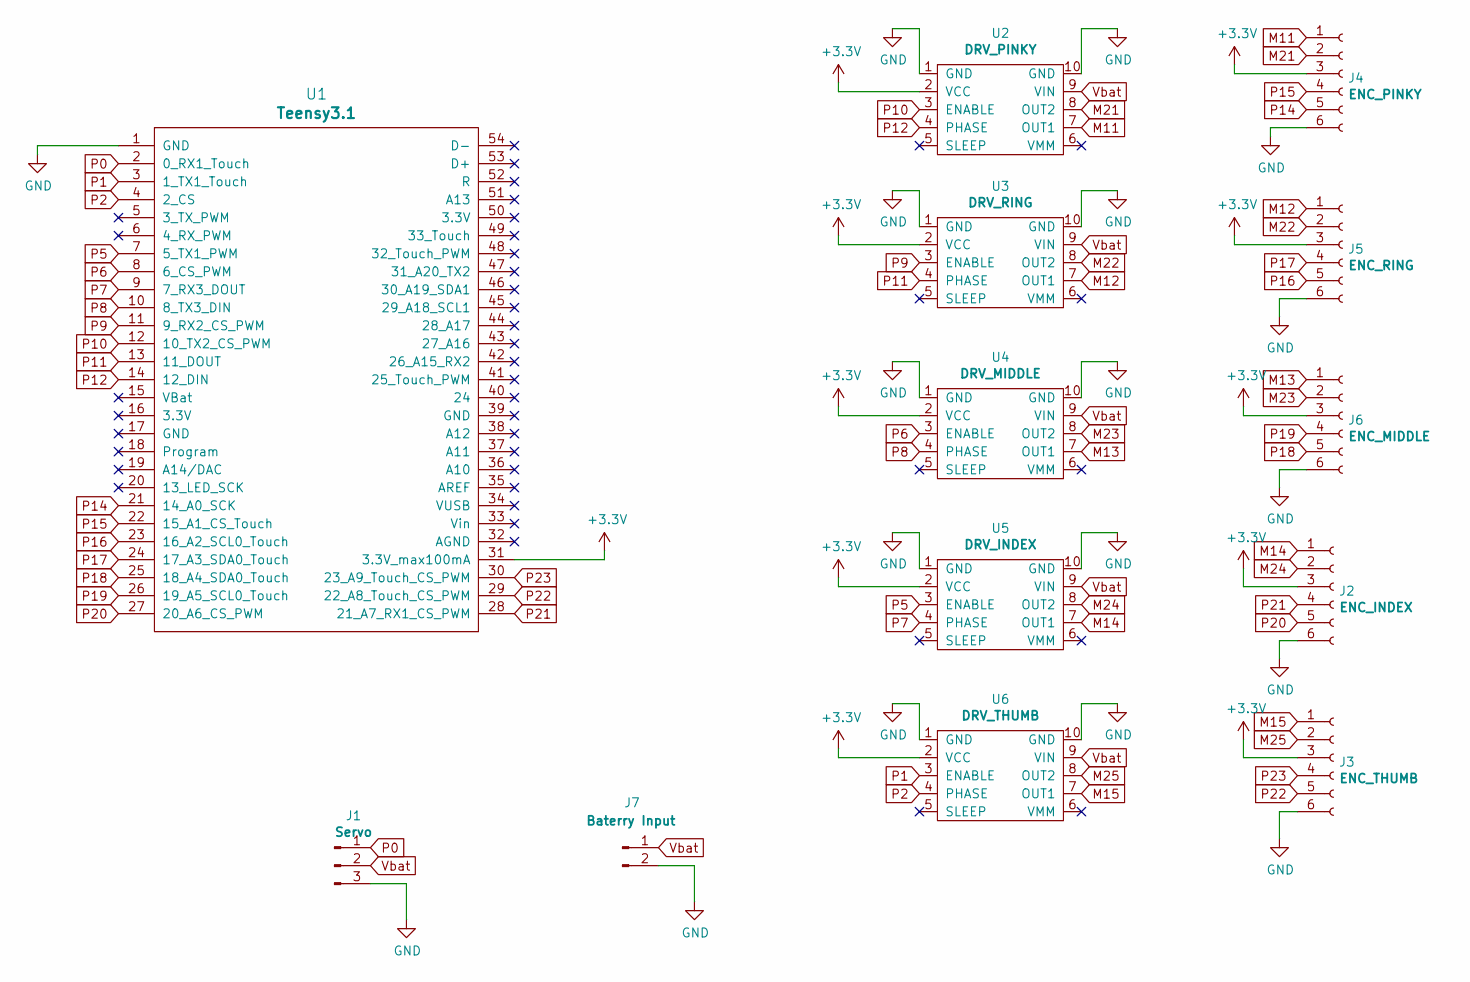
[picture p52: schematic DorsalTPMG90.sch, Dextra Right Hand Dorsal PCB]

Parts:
J1: Servo; PinHeader_1x03_P2.54mm_Vertical
J2: ENC_INDEX; PinHeader_1x06_P2.54mm_Vertical
J3: ENC_THUMB; PinHeader_1x06_P2.54mm_Vertical
J4: ENC_PINKY; PinHeader_1x06_P2.54mm_Vertical
J5: ENC_RING; PinHeader_1x06_P2.54mm_Vertical
J6: ENC_MIDDLE; PinHeader_1x06_P2.54mm_Vertical
J7: Baterry Input; PinHeader_1x02_P2.54mm_Vertical
U1: Teensy3.1; Teensy31_32_SidesOnly
U2: DRV_PINKY; Pololu_DRV8838
U3: DRV_RING; Pololu_DRV8838
U4: DRV_MIDDLE; Pololu_DRV8838
U5: DRV_INDEX; Pololu_DRV8838
U6: DRV_THUMB; Pololu_DRV8838

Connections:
+3V3: J2.3, J3.3, J4.3, J5.3, J6.3, U1.31 (3.3V_max100mA), U2.2 (VCC), U3.2 (VCC), U4.2 (VCC), U5.2 (VCC), U6.2 (VCC)
GND: J1.3, J2.6, J3.6, J4.6, J5.6, J6.6, J7.2, U1.1 (GND), U2.1 (GND), U2.10 (GND), U3.1 (GND), U3.10 (GND), U4.1 (GND), U4.10 (GND), U5.1 (GND), U5.10 (GND), U6.1 (GND), U6.10 (GND)
M11: J4.1, U2.7 (OUT1)
M12: J5.1, U3.7 (OUT1)
M13: J6.1, U4.7 (OUT1)
M14: J2.1, U5.7 (OUT1)
M15: J3.1, U6.7 (OUT1)
M21: J4.2, U2.8 (OUT2)
M22: J5.2, U3.8 (OUT2)
M23: J6.2, U4.8 (OUT2)
M24: J2.2, U5.8 (OUT2)
M25: J3.2, U6.8 (OUT2)
P0: J1.1, U1.2 (0_RX1_Touch)
P1: U1.3 (1_TX1_Touch), U6.3 (ENABLE)
P2: U1.4 (2_CS), U6.4 (PHASE)
P5: U1.7 (5_TX1_PWM), U5.3 (ENABLE)
P6: U1.8 (6_CS_PWM), U4.3 (ENABLE)
P7: U1.9 (7_RX3_DOUT), U5.4 (PHASE)
P8: U1.10 (8_TX3_DIN), U4.4 (PHASE)
P9: U1.11 (9_RX2_CS_PWM), U3.3 (ENABLE)
P10: U1.12 (10_TX2_CS_PWM), U2.3 (ENABLE)
P11: U1.13 (11_DOUT), U3.4 (PHASE)
P12: U1.14 (12_DIN), U2.4 (PHASE)
P14: J4.5, U1.21 (14_A0_SCK)
P15: J4.4, U1.22 (15_A1_CS_Touch)
P16: J5.5, U1.23 (16_A2_SCL0_Touch)
P17: J5.4, U1.24 (17_A3_SDA0_Touch)
P18: J6.5, U1.25 (18_A4_SDA0_Touch)
P19: J6.4, U1.26 (19_A5_SCL0_Touch)
P20: J2.5, U1.27 (20_A6_CS_PWM)
P21: J2.4, U1.28 (21_A7_RX1_CS_PWM)
P22: J3.5, U1.29 (22_A8_Touch_CS_PWM)
P23: J3.4, U1.30 (23_A9_Touch_CS_PWM)
Vbat: J1.2, J7.1, U2.9 (VIN), U3.9 (VIN), U4.9 (VIN), U5.9 (VIN), U6.9 (VIN)

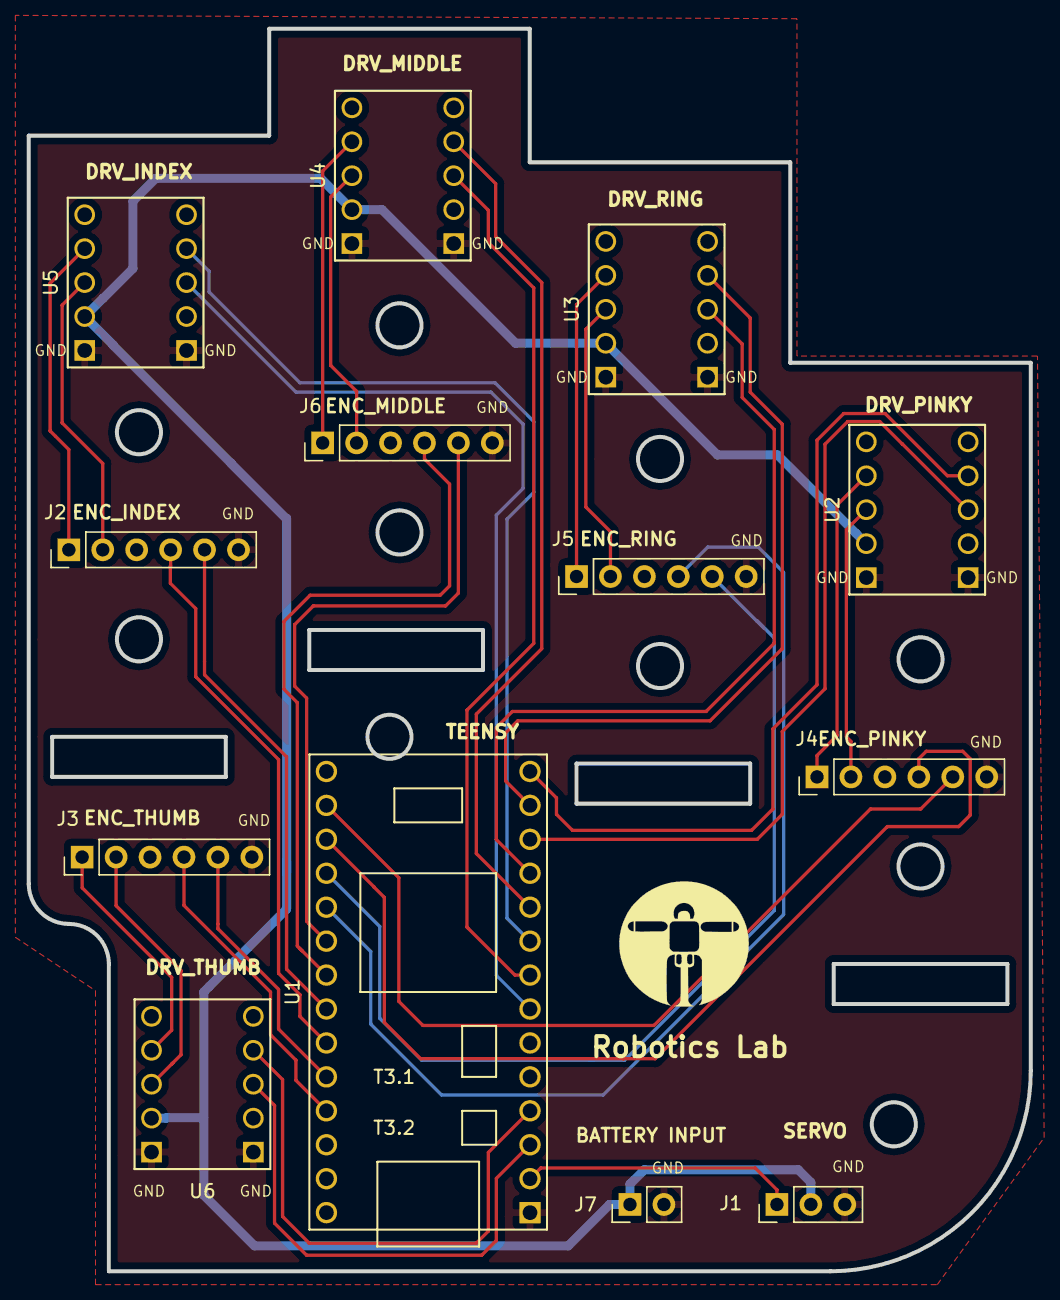
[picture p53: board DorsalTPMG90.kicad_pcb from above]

Board: 2 copper layers, 75.0 x 93.0 mm, 13 parts (0 on the bottom side), 34 nets.

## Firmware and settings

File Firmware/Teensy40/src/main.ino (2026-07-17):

#include <Arduino.h>
#include <Finger.h>
#include <Synapse.h>
#include <Servo.h>
#include <MsTimer2.h>

#define pidTime 10 // ms
#define tr 379.17

// phase, enable, A, B
Finger thumb(22, 23, 21, 20, tr);
Finger indx(14, 15,17,16, tr);
Finger middle(12, 13,11,10, tr);
Finger ring(8, 9,7,6, tr);
Finger pinky(4, 5,3,2, tr);

Servo abductor;

Synapse dataLink(Serial);

float abductorAngle = map(10, 0, 90, 20, 110);

void handControl() {
    thumb.positionPID();
    indx.positionPID();
    middle.positionPID();
    ring.positionPID();
    pinky.positionPID();
}

void thumbReadEncoder() {
    thumb.readEncoder();
}

void indexReadEncoder() {
    indx.readEncoder();
}

void middleReadEncoder() {
    middle.readEncoder();
}

void ringReadEncoder() {
    ring.readEncoder();
}

void pinkyReadEncoder() {
    pinky.readEncoder();
}

void setup() {
    attachInterrupt(digitalPinToInterrupt(thumb.getEncoderPinA()), thumbReadEncoder, CHANGE);
    attachInterrupt(digitalPinToInterrupt(indx.getEncoderPinA()), indexReadEncoder, CHANGE);
    attachInterrupt(digitalPinToInterrupt(middle.getEncoderPinA()), middleReadEncoder, CHANGE);
    attachInterrupt(digitalPinToInterrupt(ring.getEncoderPinA()), ringReadEncoder, CHANGE);
    attachInterrupt(digitalPinToInterrupt(pinky.getEncoderPinA()), pinkyReadEncoder, CHANGE);

    abductor.attach(19);
    abductor.write(abductorAngle);

    MsTimer2::set(pidTime, handControl);
    MsTimer2::start();

    Serial.begin(115200);

    pinMode(13, OUTPUT);
    digitalWrite(13, LOW);
}

void loop() {
    float setPointArray[6];

    dataLink.readSetPoints(&setPointArray[0]);

    abductorAngle = map(setPointArray[0], 0, 90, 20, 110);
    abductor.write(abductorAngle);

    thumb.writePosition(setPointArray[1]);
    indx.writePosition(setPointArray[2]);
    middle.writePosition(setPointArray[3]);
    ring.writePosition(setPointArray[4]);
    pinky.writePosition(setPointArray[5]);
}

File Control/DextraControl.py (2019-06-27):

from kivy.app import App
from kivy.uix.tabbedpanel import TabbedPanel
from kivy.properties import ObjectProperty, ListProperty
from kivy.clock import Clock

import time
import synapse

class RootWidget(TabbedPanel):
    ser = None
    scheduled_event = None
    setpoint_list = ListProperty([0.0, 0.0, 0.0, 0.0, 0.0, 0.0])
    serial_port_list = ListProperty([])
    devices = ObjectProperty(None)
    status = ObjectProperty(None)

    def scan_ports(self):
        if not self.status.value:
            self.devices.text = "Select device"
            self.serial_port_list = synapse.scan_serial_ports()

    def connect(self):
        if not self.status.value:
            self.ser, self.status.value = synapse.connect_to_serial(self.devices.text)
            if self.status.value:
                # self.scheduled_event = Clock.schedule_interval(self.send_setpoint_list, 0.1)
                self.status.text = "Connected"
                self.status.color = [0,1,0,1]
            else:
                self.status.text = "No serial port found"
                self.status.color = [1,0,0,1]

    def disconnect(self):
        if self.status.value:
            self.ser.close()
            # Clock.unschedule(self.scheduled_event)
            self.status.value = False
            self.status.text = "Disconnected"
            self.status.color = [1,1,0,1]
        else:
            self.status.text = "Not connected"
            self.status.color = [1,0,0,1]

    def send_setpoint_list(self,dt):
        try:
            synapse.write_setpoint_list(self.ser,self.setpoint_list)
            # print self.setpoint_list
        except:
            # Clock.unschedule(self.scheduled_event)
            self.status.value = False
            self.status.text = "Transmission error"
            self.status.color = [1,0,0,1]

class DextraControlApp(App):
    def build(self):
        return RootWidget()

if __name__ == '__main__':
    DextraControlApp().run()

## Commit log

2018-03-05 Dextra TPMG90-1 CAD files
    Modified CAD files from original Dextra robotic hand files to adapt them to TowerPro MG90 servomotor
    [abductorTPMG90-1.FCStd, abductorTPMG90-1.stl, dorsalTPMG90-1.FCStd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]
2018-07-01 Dextra TPMG90-2 CAD files
    [distalTPMG90-2.FCStd, dorsalTPMG90-2.FCStd, palmTPMG90-2.FCStd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]
2018-07-01 Create Schematics
2018-07-01 DEXTRA Schematics
2018-07-01 Left hand CAD files
2018-07-01 Dextra ORIGINAL CAD files
    [abductor.fcstd, distal.fcstd, distal_thumb.fcstd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]
2018-10-10 add missing file
    [distal_tumbTPMG90-2.FCStd]
2019-06-27 Adjust pinout to new PCB
2019-06-27 Add udev rules
    https://www.pjrc.com/teensy/tutorial.html
2019-06-27 Adjust encoder limits and initial pose
2026-04-14 Embrace bytearray in modern pySerial, fix style
    [synapse.py]
